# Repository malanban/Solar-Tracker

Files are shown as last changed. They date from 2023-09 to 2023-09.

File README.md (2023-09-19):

# Solar-Tracker
##Abstract
The objective of the project automatic solar tracker is to design and build a PID controller to rotate a solar panel which is capable of dynamically adjusting the solar panel to achieve its highest efficiency. The feedback error control mechanism is established using PID to adjust the PWM signal. The PWM signal controls the speed and the direction of rotation of the motor which is connected to the axis of the solar panel. Two LDRs are fixed symmetrically at both sides of the solar panel. These LDRs are producing the error which says how much the solar panel is deviated from its best efficiency position.

## Design Specifications
Complete design is based on analog electronics components. (Operational Amplifiers, capacitors, resistors)
Single axis design
1 second maximum latency to track the sunlight and adjust the panel. 
dynamically adjusting the panel’s angular position to achieve the highest efficiency. 

## Method
### i. Input

The solar tracker comprises 2 LDR sensors placed at either ends of the panel. The potential at the midpoint between the 2 LDRs is subject to change depending on the intensity of light falling on each of them. This value is compared with the set point ( the value obtained if both LDRs receive the same amount of light ), and the difference (error) between the 2 readings is calculated using a differential amplifier.


### ii. PID control- proportional integral differential

The error obtained is fed into the PID control circuit. The PID control circuit acts as a feedback system that will adjust the panel’s orientation depending on the error calculated. It comprises of 3 operational amplifiers configured to perform proportional, integral and derivative operations.

Proportional: The proportional part gives a gain to the error signal. Here an inverting op amp configuration is used to get the required gain, including variable resistors to adjust the gain of the error to the required value.



Integral: The integral part reduces the steady state error by accumulating the error over time. An op amp integrator is used for this task with variable resistors. Here the 1Mohm resistor is used in parallel with the capacitor of the integrator to prevent the integration of input offset voltage of the op amp and producing an incorrect output.



Derivative: The derivative component produces the output signal proportional to the rate of change of the error. It reduces the overshoot and smoothens the control signal. An op amp differentiator circuit is used here including variable resistors to adjust the values. There is a resistor series to the capacitor of the differentiator to decrease the effects of noise by decreasing the high frequency gain.



### iii. PWM generation

Square wave generation

The first part of this circuit is the schmitt trigger circuit, then comes the integrator circuit. The schmitt trigger circuit is basically a comparator circuit. When the non inverting input rises or falls about the inverting input, the output of the schmitt trigger will be the two saturated supply voltages.

Triangular wave generation

This output is applied to the integrator circuit and it integrates this voltage for a finite time. The output of the integrator circuit is fed back as input into the schmitt trigger.PWM wave generation
The comparator output will be a PWM signal whose pulse width will vary depending on the error.

 

### iv. Motor controller

Built using L293D

### v. Component Selection

Motor Selection

Motor designs for solar power applications, therefore, must stand up to extremes in temperature (both absolute and over a broad range), humidity and highly corrosive salt sprays, wind loads and abrasive airborne particulate matter. Our choice- Brushed DC motors- simple, easy driving method and low cost. Control of dc motor is complex and life is short but we can replace brushes. As the solar panel can be affected by wind power high power motor is selected according to its weight and dimensions.
Selected motor – brushed dc motor
Voltage -12V
No load speed- 25 RPM
No load current- 60mA
Max torque- 16 kgcm
Stall current-0.9 A

Motor driver selection
According to our motor it drives a stall current of 0.9 A . so the maximum current of the motor driver should be greater than 0,9 A. Logic voltage as 5 V. our solar panel is in medium size (22 cm x 14 cm) , L93D is used.Op amp selection
LM741 (General Purpose)
LM339N (For Comparator)
LMC 560 (For Buffer)

## Circuit Diagram


## Enclosure



## PCB
After testing the circuit in breadboards and obtaining the desired output waveforms, the PCB was designed using Altium software for the final implementation. The output Gerber files were generated and sent to China (JLCPCB) for printing.




Link for JLCPCB: https://jlcpcb.com/
## Our Product


## Our Team
Amarasinghe A.M.V.M.

Gunawardena M.N.

Malanban K.

Rathnayake R.N.P

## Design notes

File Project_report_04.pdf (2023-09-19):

## University of Moratuwa Faculty of Engineering Department of Electronic & Telecommunication Engineering

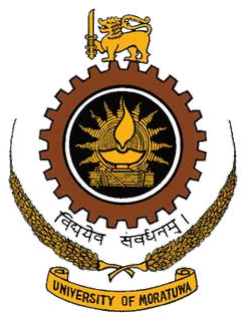
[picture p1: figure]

EN2091 -Laboratory Practice and Projects

Group 04 -Automatic Solar Tracker

Project report

AMARASINGHE A.M.V.M. | 200027R
GUNAWARDENA M.N. | 200201V
MALANBAN K. | 200373X
RATHNAYAKE R.N.P. | 200537F

## Contents

1 Introduction | 2
2 Method | 2
3 Results | 9
4 Individual contributions of each group member | 10
5 | Conclusion & Future Works | 10
6 Acknowledgement | 10
7 References / Bibliography | 10
8 Appendix-I Data Sheet | 11

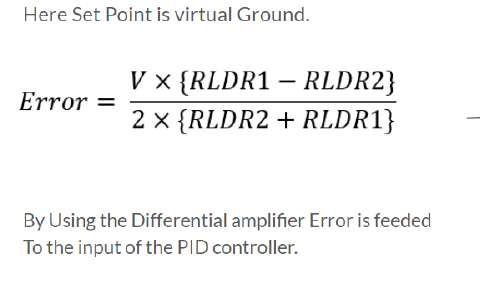
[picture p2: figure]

## Abstract

The objective of the project automatic solar tracker is to design and build a PID controller to rotate a solar panel which is capable of dynamically adjusting the solar panel to achieve its highest efficeincy. The feedback error control mechanism is established using PID to adjust the PWM signal. The PWM signal controls the speed and the direction of rotation of the motor which is connected to the axis of the solar panel. Two LDRs are fixed symmetrically at both sides of the solar panel. These LDRs are producing the error which says how much the solar panel is deviated from its best efficiency position.

## 1 Introduction

The energy industry is shifting towards renewable forms of energy due to the economic, environmental and social benefits it has over traditional energy sources. Solar energy is a major source of renewable energy that is mainly harvested through solar panels. The orientation of solar panels is vital for it to receive a high intensity of light. Since the direction of sunlight falling on the panels can vary through the course of the day, a fixed orientation is not ideal. The purpose of this project is to design an automatic solar tracker that is capable of rotating the solar panel such that it receives the maximum intensity of light. Most modern solar trackers are built with digital electronics with the use of PID concepts. The objective is to design a similar solar tracker using analog electronics with a PID control circuit.

## 2 Method

### 2.1 Functionality

### 2.1.1 Input

The solar tracker comprises 2 LDR sensors placed at either ends of the panel. The potential at the midpoint between the 2 LDRs is subject to change depending on the intensity of light falling on each of them. This value is compared with the set point ( the value obtained if both LDRs receive the same amount of light ), and the difference (error) between the 2 readings is calculated using a differential amplifier.

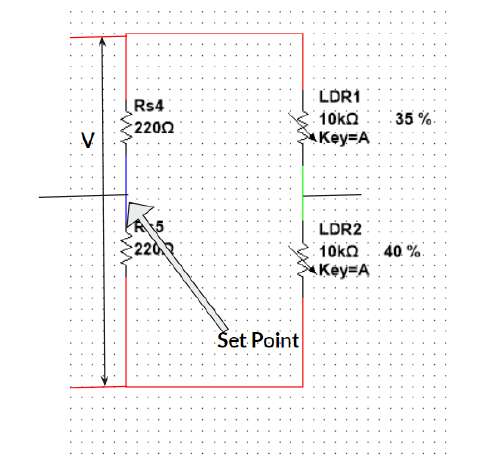
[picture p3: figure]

Figure 1: Input part

### 2.1.2 PID Control

The error obtained is fed into the PID control circuit. The PID control circuit acts as a feedback system that will adjust the panel’s orientation depending on the error calculated. It comprises of 3 operational amplifiers configured to perform proportional, integral and derivative operations.
- Propotional The proportional part gives a gain to the error signal. Here an inverting op amp configuration is used to get the required gain, including variable resistors to adjust the gain of the error to the required value.

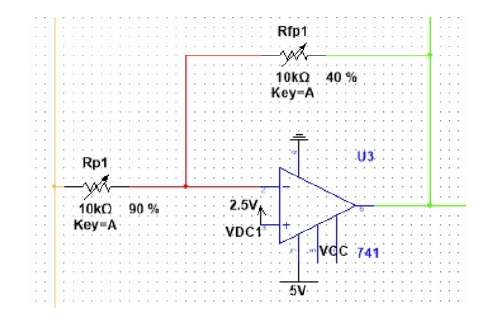
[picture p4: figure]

Figure 2: Propotional part

- Integral
The integral part reduces the steady state error by accumulating the error over time. An op amp integrator is used for this task with variable resistors. Here the 1Mohm resistor is used in parallel with the capacitor of the integrator to prevent the integration of input offset voltage of the opamp and producing an incorrect output.

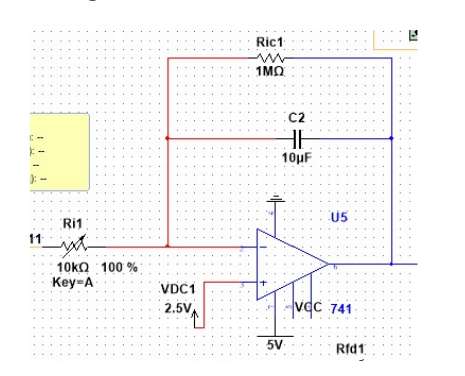
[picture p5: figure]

Figure 3: Integral part

- Derivative
The derivative component produces the output signal proportional to the rate of change of the error. It reduces the overshoot and smoothens the control signal. An op amp differentiator circuit is used here including variable resistors to adjust the values. There is a resistor series to the capacitor of the differentiator to decrease the effects of noise by decreasing the high frequency gain.

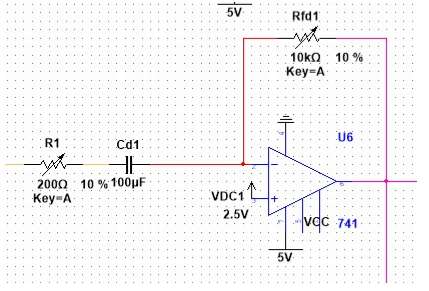
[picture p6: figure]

Figure 4: Derivative part

The outputs of the proportional, integral and differential components are connected to an adder circuit using variable resistors. These resistors are used to adjust the Kp, Ki, Kd values.

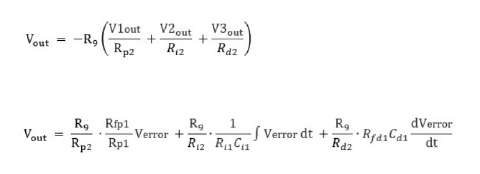
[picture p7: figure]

### 2.1.3 Triangular Waveform Generation

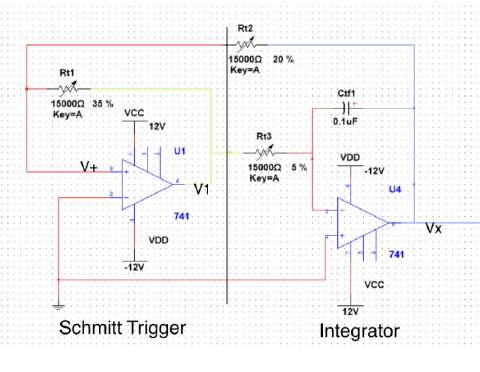
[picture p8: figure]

Figure 5: Triangular Wave Generation Circuit

The motor is fed a PWM signal to control its rotation. To generate the PWM signal, a triangular waveform is used. To generate this triangular waveform, a squarewave is first produced followed by an integrator circuit.
The first part of this circuit is the schmitt trigger circuit, then comes the integrator circuit. The schmitt trigger circuit is basically a comparator circuit. When the non inverting input rises or falls about the inverting input, the output of the schmitt trigger will be the two saturated supply voltages. This output is applied to the integrator circuit and it integrates this voltage for a finite time. The output of the integrator circuit is fed back as input into the schmitt trigger. Suppose initially output of schmitt trigger is +Vs. This is integrated by the integrator circuit and fed into the schmitt trigger input and when this integrated voltage crosses the lower threshold value, the output of the schmitt trigger will shift from +Vs to -Vs. Now the integrator will integrate –Vs and its value is fed into the schmitt trigger. When this crosses the upper threshold voltage, the schmitt trigger output will again shift to +Vs. Here the resulting triangular waveform will be symmetric .

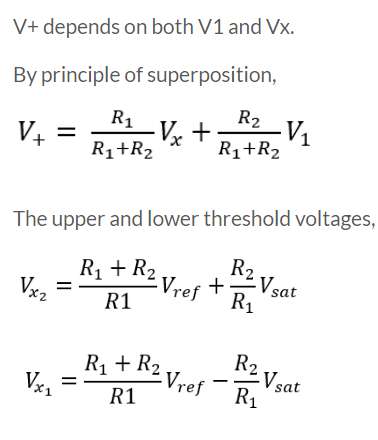
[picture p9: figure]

### 2.1.4 Motor Drive

The PID circuit output is compared with the generated triangular wave using comparators. The comparator output will be a PWM signal whose pulse width will vary depending on the error. Here, 2 comparators are used to get 2 PWM signals, which are inversions of one another. These signals are given as input to the motor driver.

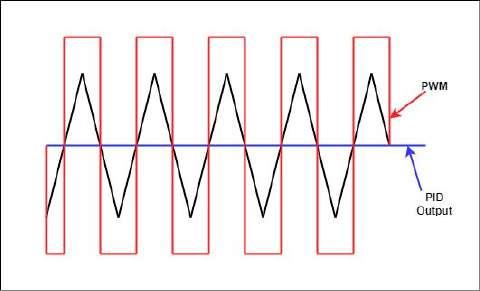
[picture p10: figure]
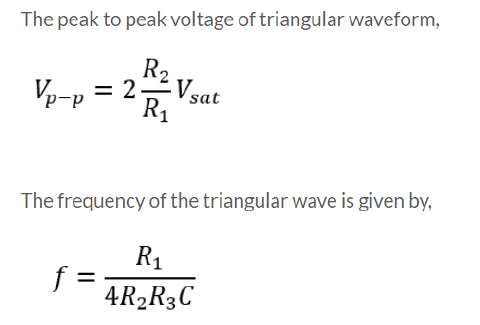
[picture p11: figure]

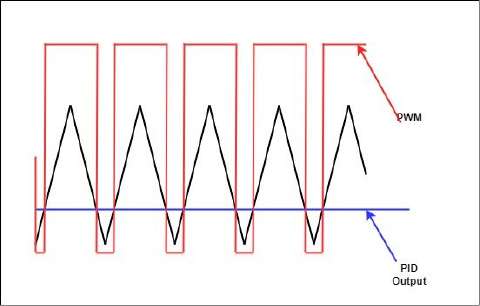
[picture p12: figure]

### 2.2 Block Diagram

### 2.3 Selection of components

### 2.3.1 Op amp selection

### 2.3.2 Motor selection

Motor designs for solar power applications, therefore, must stand up to extremes in temperature (both absolute and over a broad range), humidity and highly corrosive salt sprays, wind loads and abrasive airborne particulate matter.
Our choice- Brushed DC motors- simple, easy driving method and low cost. Control of dc motor is complex and life is short but we can replace brushes. As the solar panel can be affected by wind power high power motor is selected according to its weight and dimensions.
Selected motor - brushed dc motor
Voltage -12V
No load speed- 25 RPM
No load current- 60mA
Max torque- 16 kgcm
Stall current-0.9 A

### 2.3.3 Motor driver selection

According to our motor it drives a stall current of 0.9 A . so the maximum current of the motor driver should be greater than 0,9 A. Logic voltage os 5 V. our solar panel is in medium size (22 cm x 14 cm) , L93D is used.

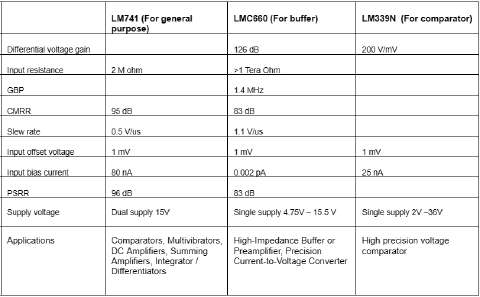
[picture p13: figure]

### 2.4 Simulation using multisim

We implemented our circuit in Multisim to test the functionality of the circuit. We updated our circuit according to the results we got from the simulation. We identify the errors and further updates using the graphs generated using multisim.

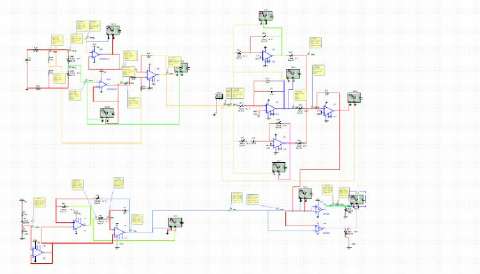
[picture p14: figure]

Figure 6: Circuit in Multisim

### 2.5 Breadboard implementation

The circuits were simulated and tested using NI Multisim simulation software. The simulated circuits were then implemented in breadboards and functionality was verified. The results obtained through the simulation and those obtained in the breadboard implementation had significant differences and slight changes had to be made to the circuit to obtain the desired results.

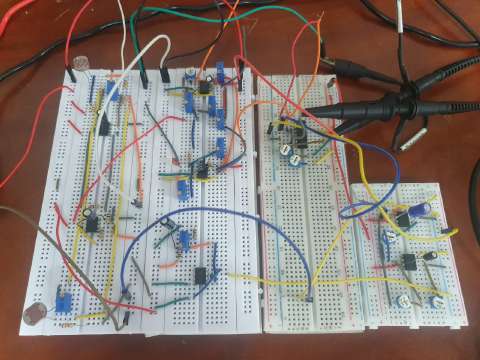
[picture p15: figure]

Figure 7: Breadboard implementation

### 2.6 Schematic

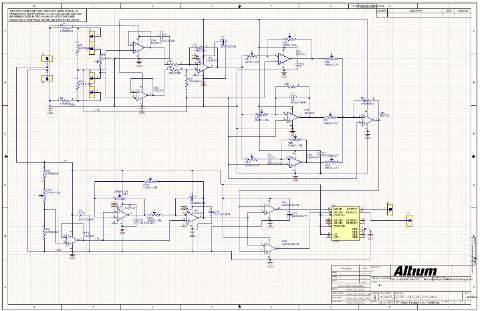
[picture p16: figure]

Figure 8: Schematic

### 2.7 PCB Design

After testing the circuit in breadboards and obtaining the desired output waveforms, the PCB was designed using Altium software for the final implementation. The output Gerber files were generated and sent to China (JLCPCB) for printing.

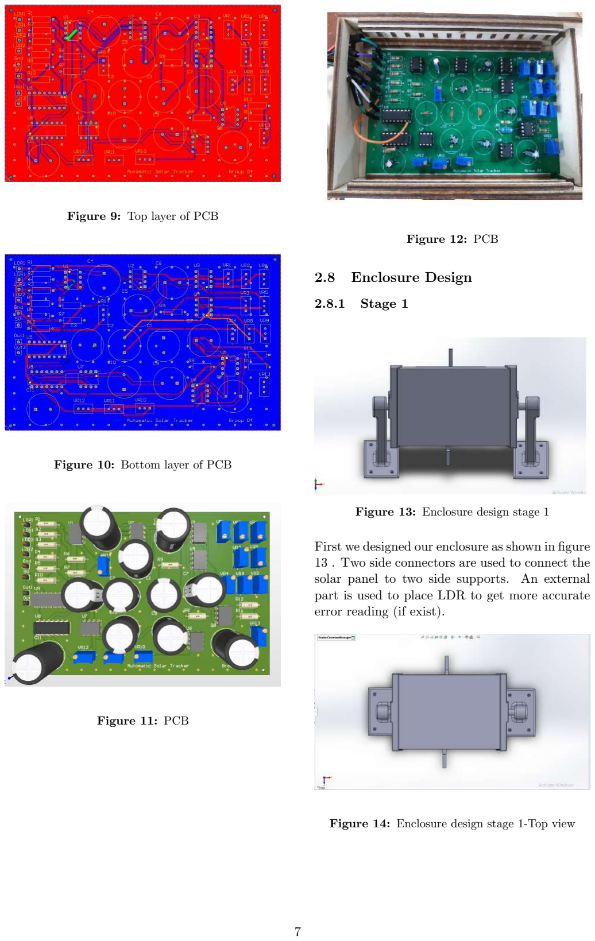
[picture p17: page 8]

Figure 9: Top layer of PCB

Figure 10: Bottom layer of PCB

Figure 11: PCB

Figure 12: PCB

### 2.8 Enclosure Design

### 2.8.1 Stage 1

Figure 13: Enclosure design stage 1

First we designed our enclosure as shown in figure 13 . Two side connectors are used to connect the solar panel to two side supports. An external part is used to place LDR to get more accurate error reading (if exist).

Figure 14: Enclosure design stage 1-Top view

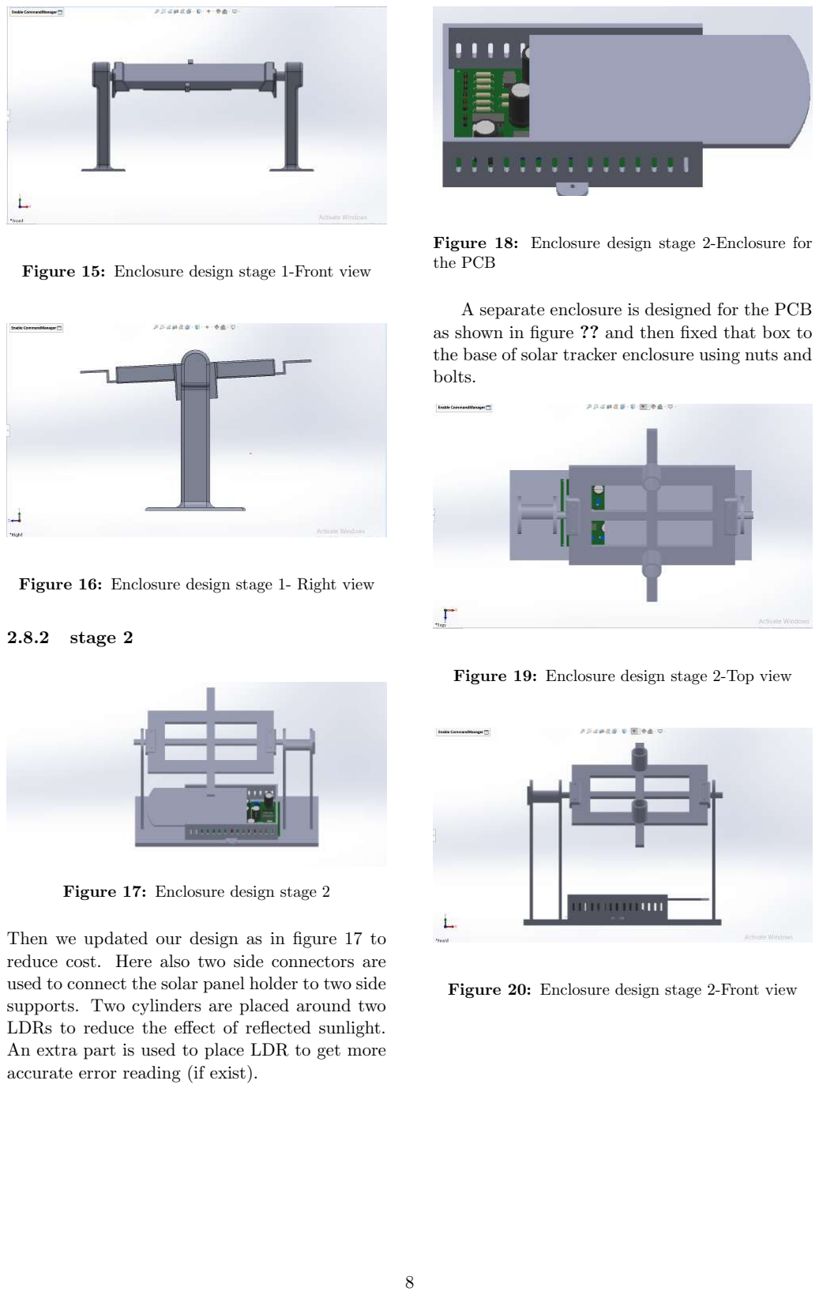
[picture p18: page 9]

Figure 15: Enclosure design stage 1-Front view

Figure 16: Enclosure design stage 1- Right view

### 2.8.2 stage 2

Figure 17: Enclosure design stage 2

Then we updated our design as in figure 17 to reduce cost. Here also two side connectors are used to connect the solar panel holder to two side supports. Two cylinders are placed around two LDRs to reduce the effect of reflected sunlight. An extra part is used to place LDR to get more accurate error reading (if exist).

Figure 18: Enclosure design stage 2-Enclosure for the PCB

A separate enclosure is designed for the PCB as shown in figure ?? and then fixed that box to the base of solar tracker enclosure using nuts and bolts.

Figure 19: Enclosure design stage 2-Top view

Figure 20: Enclosure design stage 2-Front view

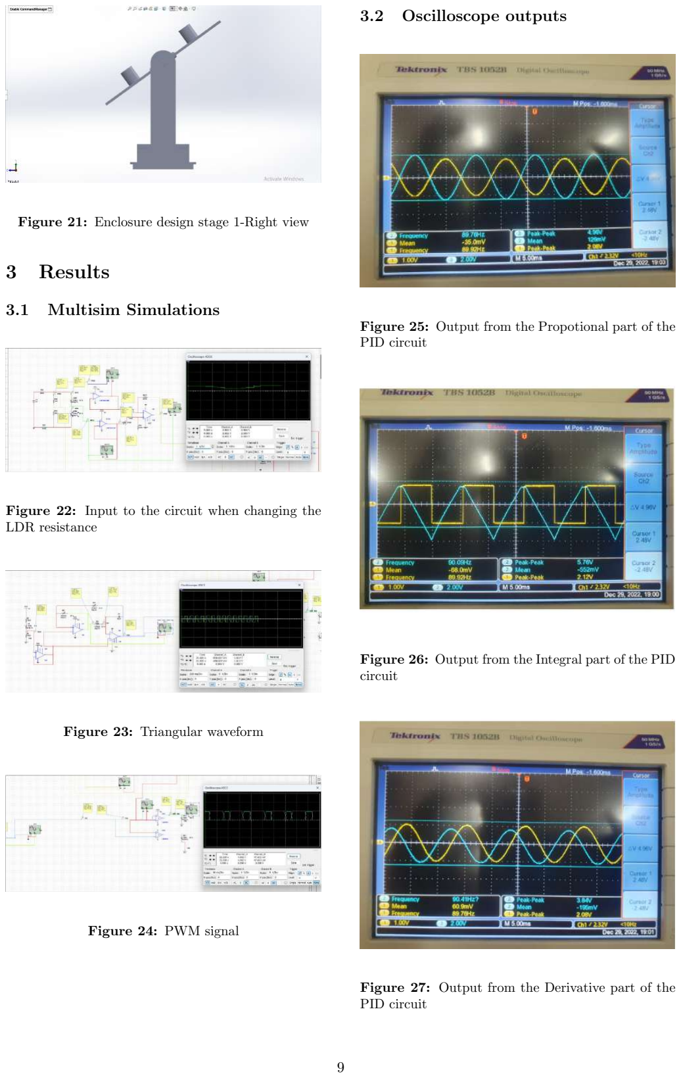
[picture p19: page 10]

Figure 21: Enclosure design stage 1-Right view

## 3 Results

### 3.1 Multisim Simulations

Figure 22: Input to the circuit when changing the LDR resistance

Figure 23: Triangular waveform

Figure 24: PWM signal

### 3.2 Oscilloscope outputs

Figure 25: Output from the Propotional part of the PID circuit

Figure 26: Output from the Integral part of the PID circuit

Figure 27: Output from the Derivative part of the PID circuit

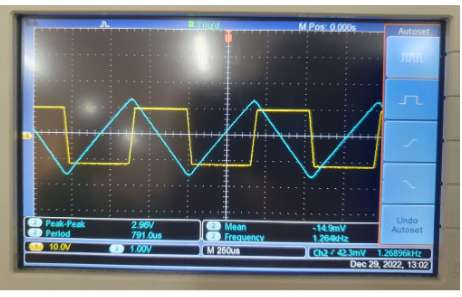
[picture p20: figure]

Figure 28: Output from the triangular waveform ganerating circuit

## 4 Individual contributions of each group member

Group Members

Name. | Contribution
AMARASINGHE A.M.V.M. (200027R ) | Enclosure design-ing (solidworks), simulation us-ing Multisim , Circuit testing, documentation, Soldering
GUNAWARDENA M.N.(200201V) | Schematic drawing (Altium), Circuit testing, Soldering , Documentation
MALANBAN K.(200373X) | Circuit designing, Circuit testing and tuning, solderin, Documentation
RATHNAYAKE R.N.P.(200537F) | PCB designing (Altium), Circuit testing , soldering, Documentation,

## 5 Conclusion & Future Works

### 5.1 Conclusion

To get a smoother rotation of the motor more tuning should be done. Since the light conditions can change according to the environment and the season of the year there is a significant amount of attention needed for tuning to have a better motion of the motor.
Also we can increase the efficiency of power generated using solar panels using this solar tracker with a less power consumption. It will help to overcome the current energy crisis.

### 5.2 Future Works

We are planning to further develop this solar tracker as it is powered up by the voltage generated by solar panels itself.
Also a method can be developed to update the user with the aid of a mobile app by keeping track of the efficiency using graphs of voltage generated by solar panels.

## 6 Acknowledgement

The direction and assistance of multiple people was one of the aspects that contributed to the project’s success. We are really grateful to Mr. Pahan, Mr. Ravindu , and Mr. Isuru, who served as our project mentors and whose constant commitment and genuine enthusiasm for our work made it possible for us to complete the project successfully. We would also like to thank the entire laboratory staff for being kind to keep the labs open for longer periods of time and for their guidance. We want to express our gratitude to everyone who helped make this project successful, no matter how tiny their contribution.

## 7 References / Bibliography

https://www.nutsvolts.com/magazine/article/thepidcontrollerpart1

## 8 Appendix-I Data Sheet

## Automatic Solar Tracker

FEATURES

- Supply Voltage - 5 V .
- Stall current of the circuit- 400 mA
- Maximum power - 2W
- Stall current of the motor- 300 mA
- Enclosure material - wood and PLA
- PCB -2 layer

APPLICATIONS

- Can used for existing solar panels to increase the efficiency.

DESCRIPTION

- Low power solar tracker

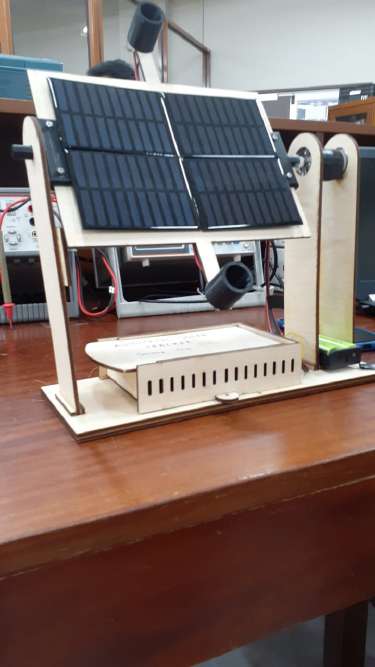
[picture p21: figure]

Figure 29: Our product

### 8.1 Appendix-II Multisim Circuit

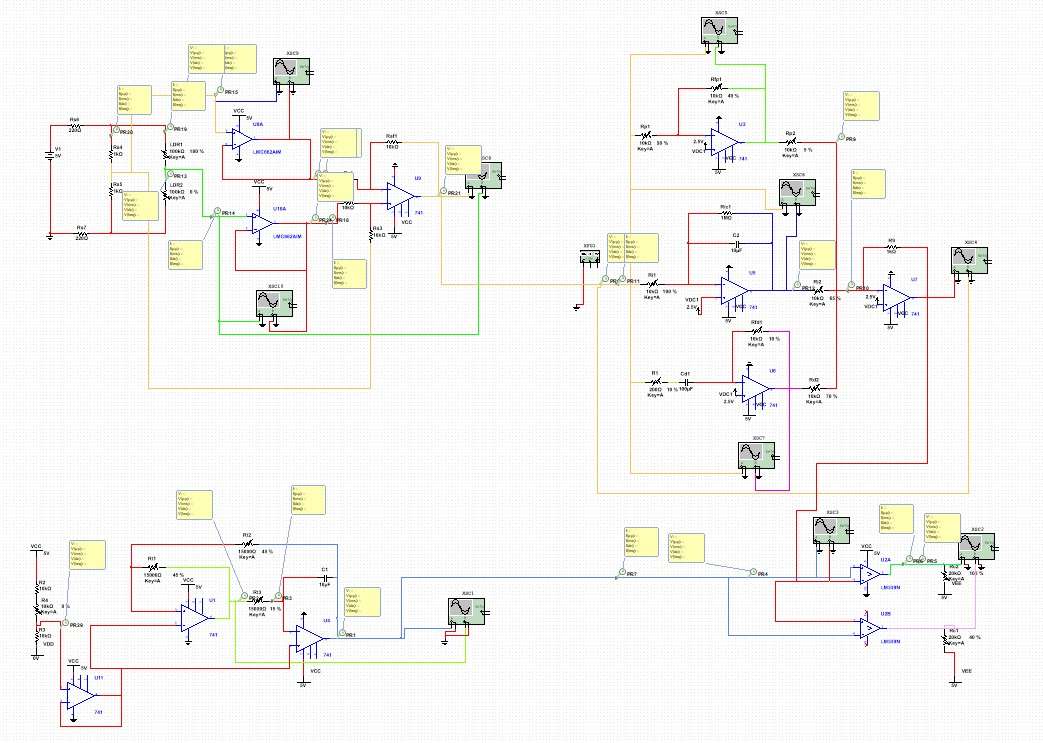
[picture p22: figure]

Figure 30: Multisim simulation Circuit

### 8.2 Appendix-III PCB Schematic

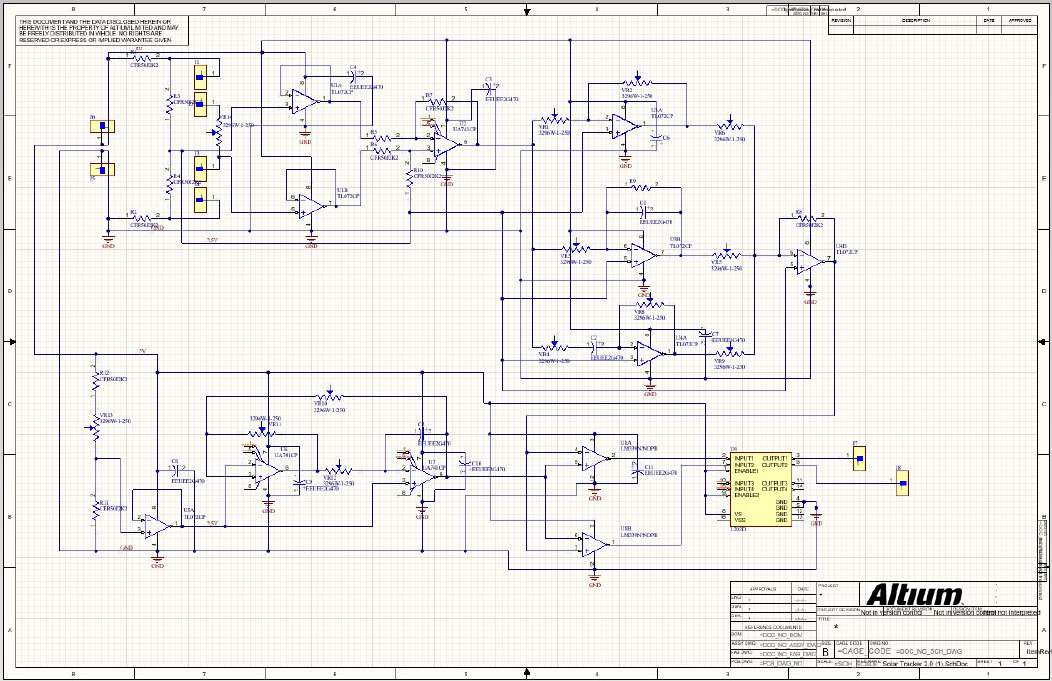
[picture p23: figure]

Figure 31: Altium schematic

### 8.3 Appendix-IV Product enclosure

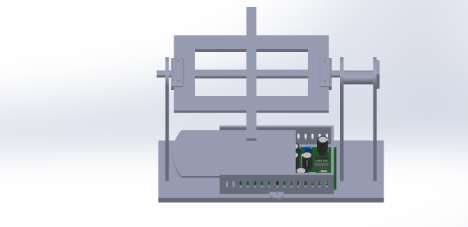
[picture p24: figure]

Figure 32: Product enclosure

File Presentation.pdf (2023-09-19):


# Automatic Solar Tracker


## Group 04

AMARASINGHE A.M.V.M. | 200027R
GUNAWARDENA M.N. | 200201V
MALANBAN K. | 200373X
RATHNAYAKE R.N.P. | 200537F

# Block Diagram of the Circuit

Power Supply 5V; LDR Input; PID Controller; Triangular wave generator; PWM generator; Motor controller & Motor; Potential divider 2.5V Output

# LDR Placement

LDR

# Feeding Error to the circuit using LDR


# LDR - GL5516 (Choosed)


- High Sensitivity
- Light Resistance (10 Lux) 5-10 KOhm
- Dark Resistance 0.5MOhm
- Fast response
- Response time 30 ms for both increasing and

decreasing
- Working Environmental temperature -30~+70

# LDR - Used

- Size 10mm
- Light Resistance arround 100 Ohm
- Dark Resistance 50-70 KOhm
- At low intensity of light resistance of LDR is

arround 4mm

# Calculations


Here Set Point is virtual Ground.

By Using the Differential amplifier Error is feeded
To the input of the PID controller. | Set Point

V

# PID Controller


### Proportional


### Integral

Ric1- Controls the DC voltage gain


### Derivative

R1- To decrease high frequency gain


PID Output

PDI

Generating the triangular waveform.

To produce the PWM signal, we compare the output of the PID circuit with a triangular wave. In producing the triangular wave, we first generate a square wave and then use an integrator circuit to get the triangular waveform.


The first part of this circuit is the schmitt trigger circuit, then comes the integrator circuit. The schmitt trigger circuit is basically a comparator circuit. When the non inverting input rises or falls about the inverting input, the output of the schmitt trigger will be the two saturated supply voltages. This output is applied to the integrator circuit and it integrates this voltage for a finite time. The output of the integrator circuit is fed back as input into the schmitt trigger.

Suppose initially output of schmitt trigger is +Vs. This is integrated by the integrator circuit and fed into the schmitt trigger input and when this integrated voltage crosses the lower threshold value, the output of the schmitt trigger will shift from +Vs to -Vs. Now the integrator will integrate –Vs and its value is fed into the schmitt trigger. When this crosses the upper threshold voltage, the output will again shift to +Vs.

Here the resulting triangular waveform will be symmetric .


V+ depends on both V1 and Vx.

By principle of superposition,

The upper and lower threshold voltages,

The peak to peak voltage of triangular waveform,

The frequency of the triangular wave is given by,

# Schematic Diagram


# PCB Design


Top layer | Bottom layer

# PCB


# Enclosure Design


1 st step of enclosure design

To reduce the cost we updated our enclosure in figure 1 to a 2nd step as shown in figure 2

Figure 1 | Figure 2

2nd step of enclosure design

holder to two side supports; c= Motor; d= To mount PCB

a= Solar panel holder - To hold the solar panels.

b= Side connectors- To connect the solar panel

## Op Amp Selection

| LM741 (For general purpose) | LMC660 (For buffer) | LM339N (For comparator)
Differential voltage gain | | 126 dB | 200 V/mV
Input resistance | 2 M ohm | >1 Tera Ohm
GBP | | 1.4 MHz
CMRR | 95 dB | 83 dB
Slew rate | 0.5 V/us | 1.1 V/us
Input offset voltage | 1 mV | 1 mV | 1 mV
Input bias current | 80 nA | 0.002 pA | 25 nA
PSRR | 96 dB | 83 dB
Supply voltage | Dual supply 15V | Single supply 4.75V – 15.5 V | Single supply 2V –36V
Applications | Comparators, Multivibrators, DC Amplifiers, Summing Amplifiers, Integrator / Differentiators | High-Impedance Buffer or Preamplifier, Precision Current-to-Voltage Converter | High precision voltage comparator


### Motor selection

Motor designs for solar power applications, therefore, must stand up to extremes in temperature (both absolute and over a broad range), humidity and highly corrosive salt sprays, wind loads and abrasive airborne particulate matter.

Our choice- Brushed DC motors- simple, easy driving method and low cost. Control of dc motor is complex and life is short but we can replace brushes. As the solar panel can be affected by wind power high power motor is selected according to its weight and dimensions.

Selected motor - brushed dc motor
Voltage -12V
No load speed- 25 RPM
No load current- 60mA
Max torque- 16 kgcm
Stall current-0.9 A

We have selected this by considering weight and dimensions of the solar panel and by comparing with other dc motors.


### Alternatives

Stepper motor-precise control and low cost . low efficiency and slow speed increase

Ac induction motors- used earlier as motor can draw current directly from the grid but controlling these motors at slow speeds is difficult. For most solar tracking purposes slow speed is necessary. So not efficient.

Servo motors- the speed variation is less in servo motors

BLDC motor (with planetary gear box) – maintenance free, have a low TCO, has no wear prone brushes, highly efficient. hits 300 rpm. High power. Easy to control. Prize is hgh.

PMDC –efficient than AC induction motors. If properly build they can last a long time up to 5000 hr continuous duty. Drawback- life of carbon brush .

### Selecting a motor driver

According to our motor it drives a stall current of 0.9 A . so the maximum current of the motor driver should be greater than 0,9 A. Logic voltage os 5 V. our solar panel is in medium size (22 cm x 14 cm) , L293D is used.


●

# Design Parameters

Operating voltage= 5v
PCB | = | 2 layer (designed) and then manufactured by JLC (china)
Stall current of the motor= 300 mA
Motor driver | = L293D
Op Amps used | = UA741CP, TL072CP , LM339N
Enclosure material = wood and PLA

# Individual contribution

AMARASINGHE A.M.V.M. 200027R = Enclosure designing (solidworks), simulation ,

GUNAWARDENA M.N. | 200201V = Schematic drawing (Altium), Circuit testing, Soldering , Documentation
MALANBAN K. | 200373X = Circuit designing, Circuit testing , soldering
RATHNAYAKE R.N.P. | 200537F = PCB designing (Altium), Circuit testing , soldering

, Circuit testing, documentation. Soldering

Documentation

Documentation

# Future Updates

1. Power up the solar tracker using the voltage generated by solar panels.
2. Keeping track of the efficiency using graphs of voltage generated by solar panels and update the user using a mobile app.

# Conclusion

To get a smooth motion more tuning should be done.

We can increase the efficiency of power generated using solar panels using this solar tracker with a less power consumption.

It will help to overcome the current energy crisis

# THANK YOU!

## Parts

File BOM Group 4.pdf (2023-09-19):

BOM _ Automatic Solar Tracker _ Group 04

Components = 4000

3D printing = 1800

Laser cutting = 3040

PCB designing = 7000

Total cost = 15840

1

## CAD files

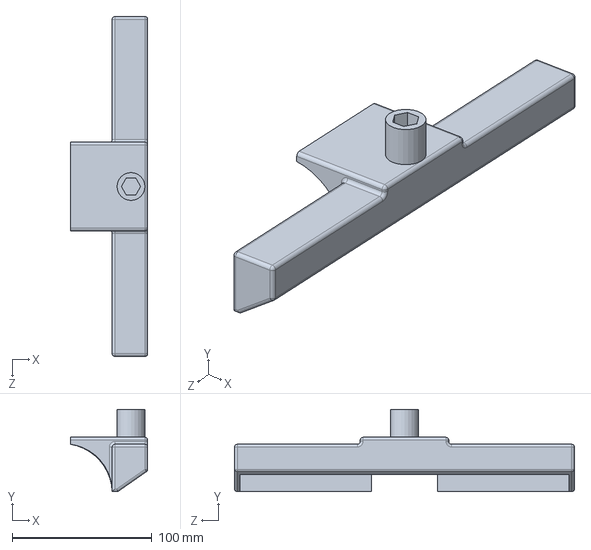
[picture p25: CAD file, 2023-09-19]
Enclosure _stage1/panel-connector-motorside.SLDPRT
55.5 x 59.0 x 243.5 mm

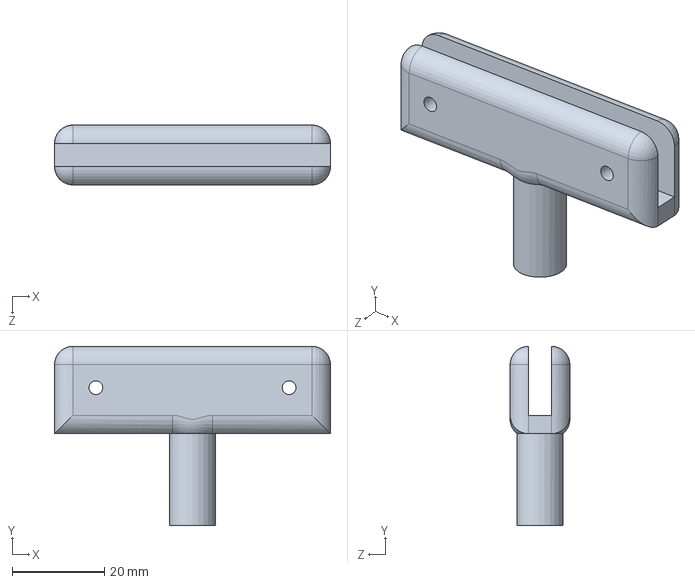
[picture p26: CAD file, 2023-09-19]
Enclosure_stage2/side connector.SLDPRT
60.0 x 39.0 x 13.0 mm

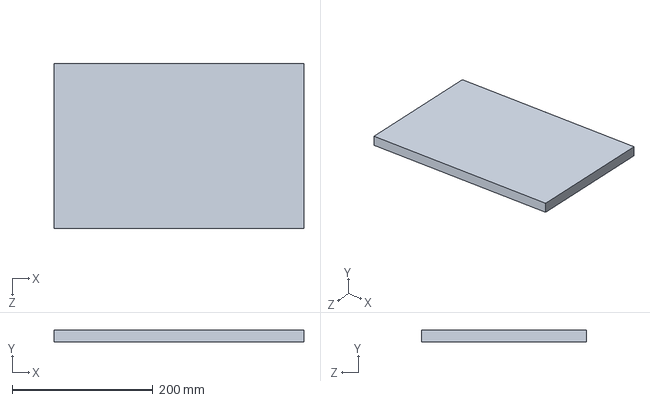
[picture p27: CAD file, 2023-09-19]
Enclosure _stage1/panel sample.SLDPRT
355.0 x 17.0 x 234.0 mm

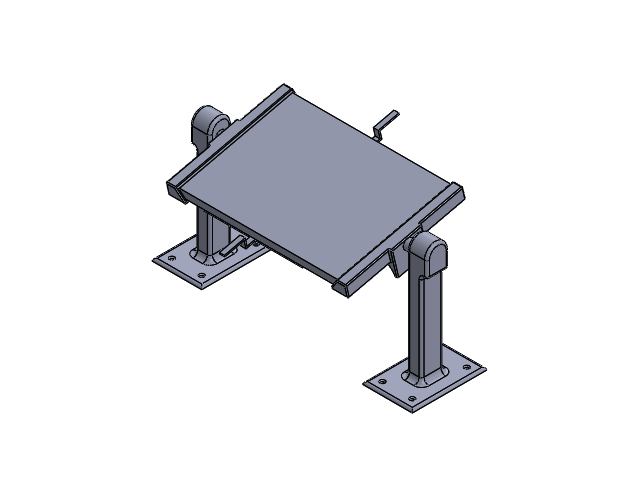
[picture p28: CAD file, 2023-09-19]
Enclosure _stage1/solar tracker stand.SLDASM
panel-connector-free side
solartracker - free side
panel sample
panel-connector-motorside
solartracker
motor part
ldr connector x 2

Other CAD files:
Enclosure_stage2/VR8.step.SLDASM
Enclosure_stage2/VR10.step.SLDASM
Enclosure_stage2/VR9.step.SLDASM
Enclosure_stage2/VR4.step.SLDASM
Enclosure_stage2/VR3.step.SLDASM
Enclosure_stage2/VR12.step.SLDASM
Enclosure_stage2/VR13.step.SLDASM
Enclosure_stage2/VR11.step.SLDASM
Enclosure_stage2/VR6.step.SLDASM
Enclosure_stage2/VR1.step.SLDASM
Enclosure_stage2/VR5.step.SLDASM
Enclosure_stage2/VR14.step.SLDASM
Enclosure_stage2/VR2.step.SLDASM
Enclosure_stage2/Extruded-6.step.SLDPRT
Enclosure _stage1/ldr connector - 2.SLDPRT
Enclosure _stage1/ldr connector.SLDPRT
Enclosure _stage1/motor part.SLDPRT
Enclosure _stage1/panel-connector-free side.SLDPRT
Enclosure _stage1/solar tracker stand - Copy.SLDASM
Enclosure _stage1/solartracker - free side.SLDPRT
Enclosure _stage1/solartracker.SLDPRT
Enclosure_stage2/Extruded-0.step.SLDPRT
Enclosure_stage2/Extruded-5.step.SLDPRT
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
